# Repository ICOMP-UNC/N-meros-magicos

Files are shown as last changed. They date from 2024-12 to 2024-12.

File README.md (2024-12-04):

# N-meros-magicos
## Control automático de compuerta y monitoreo del entorno

Este proyecto consiste en el control automático de una compuerta a través de un sensor de temperature, configurable mediante comunicación UART.

El control de la compuerta se realiza por medio de un motor paso a paso a lazo abierto.
El monitoreo del entorno se realiza por medio de un sensor de temperatura
La comunicación por UART permite el control de la compuerta, la configuración del funcionamiento del automatismo y la lectura del historial de temperaturas registradas por el sensor.

El proyecto fue diseñado originalmente para un microcontrolador LPC1769, aunque debió ser migrado durante el desarrollo a STM32F103CB, debido a la falta de disponibilidad del primer micro.

### Escenario
En un depósito de sustancias peligrosas se busca tener el control de una compuerta que permita mantenerla cerrada si la temperatura dentro del depósito es muy alta. En este caso, el automatismo debe accionar los mecanismos para enfriar el ambiente, siendo solo posible abrir la compuerta mediante un comando especial.

En cambio, si la temperatura está dentro del rango normal, la compuerta puede ser operada por medio de un switch local o desde una consola a distancia.

En cualquier caso la consola a distancia puede solicitar el estado de la compuerta y del sensor de temperatura

### Requerimientos

- Al iniciar el automatismo, debe verificar que la compuerta no presente obstáculos y tenga libre movimiento.
- Si la temperatura se encuentra dentro de un rango predefinido, la compuerta puede abrir o cerrarse con un mismo pulsador
- Si la temperatura supera el nivel de alerta, debe encenderse un enfriador,
- Si la temperatura supera el nivel máximo, debe encenderse la alarma sonora
- Si la temperatura supera el nivel crítico, debe cerrarse y bloquear la puerta, impidiendo que pueda abrirse local o remotamente
- Por seguridad, una vez bloqueada la puerta, solo puede volver a abrirse a través de una switch especial.
- Una consola externa debe poder monitorear permanentemente el estado del automatismo y operar la compuerta, excepto cuando la temperatura supere el nivel crítico.

### Diagrama de flujo del automatismo en general

```mermaid

flowchart
    A[Inicio] -->B[Inicializar motor]
    B --> C{Inicializacion ok?}
    C -->|No| E[Encender Alarma sonora y Luz de motor parpadenante]
    E --> I[Bucle infinito]
    I --> I
    C -->|Si| D[Abrir compuerta]
    D -->G[Habilitar sensor]
```

### Diagrama de flujo del sensor de temperatura

```mermaid
flowchart
    Sample[Tomar muestra] -->temp_ok{Temperatura mayor a TEMP_ALERTA?}
    temp_ok -->|No| enable_manual_mode[Habilitar operacion manual]
    temp_ok -->|Si| cooler_on[Encender enfriador]

    cooler_on -->is_temp_high{Temperatura mayor a TEMP_MAX?}
    is_temp_high-->|Si|alarm_on[Encender alarma sonora]
    alarm_on-->open_door[Abrir puerta]
    open_door-->notify[Notificar a consola]
    notify -->is_temp_critical{Temperatura mayor a TEMP_CRITICAL?}
    is_temp_critical-->|Si|lock[Cerrar y bloquear puerta]
```

### Diagrama de flujo de la rutina de inicio del motor

```mermaid
flowchart
    start[Rutina de inicio] -->move_left[Mover a izquierda]
    move_left-->sw_left{Sw izquierdo encontrado?}
    sw_left-->|si| move_right[Mover a derecha]
    sw_left-->|no| error[Fallo de inicio]
    move_right-->sw_right{Sw derecho encontrado?}
    sw_right-->|si| open_door[Abrir puerta]
    open_door-->Fin[Fin de rutina OK]
    sw_right-->|no| error[Fallo de inicio]

```

### Hardware necsario para la implementación

- Placa de desarrollo STM32F103CB
- Motor paso a paso 28BYJ-48 5v
- Driver para motor paso a paso ULN2003
- Sensor de temperatura LM35 (o potenciometro)
- Buzzer pasivo
- 2 Switches para fin de carrera
- 1 Switch para accionamiento manual
- 2 diodos LED
- 2 resistencias 220 ohms
- Módulo conversor serie TTL a USB
- PC con comunicación serie (se provee script menu.py)

### Diagrama de conexionado

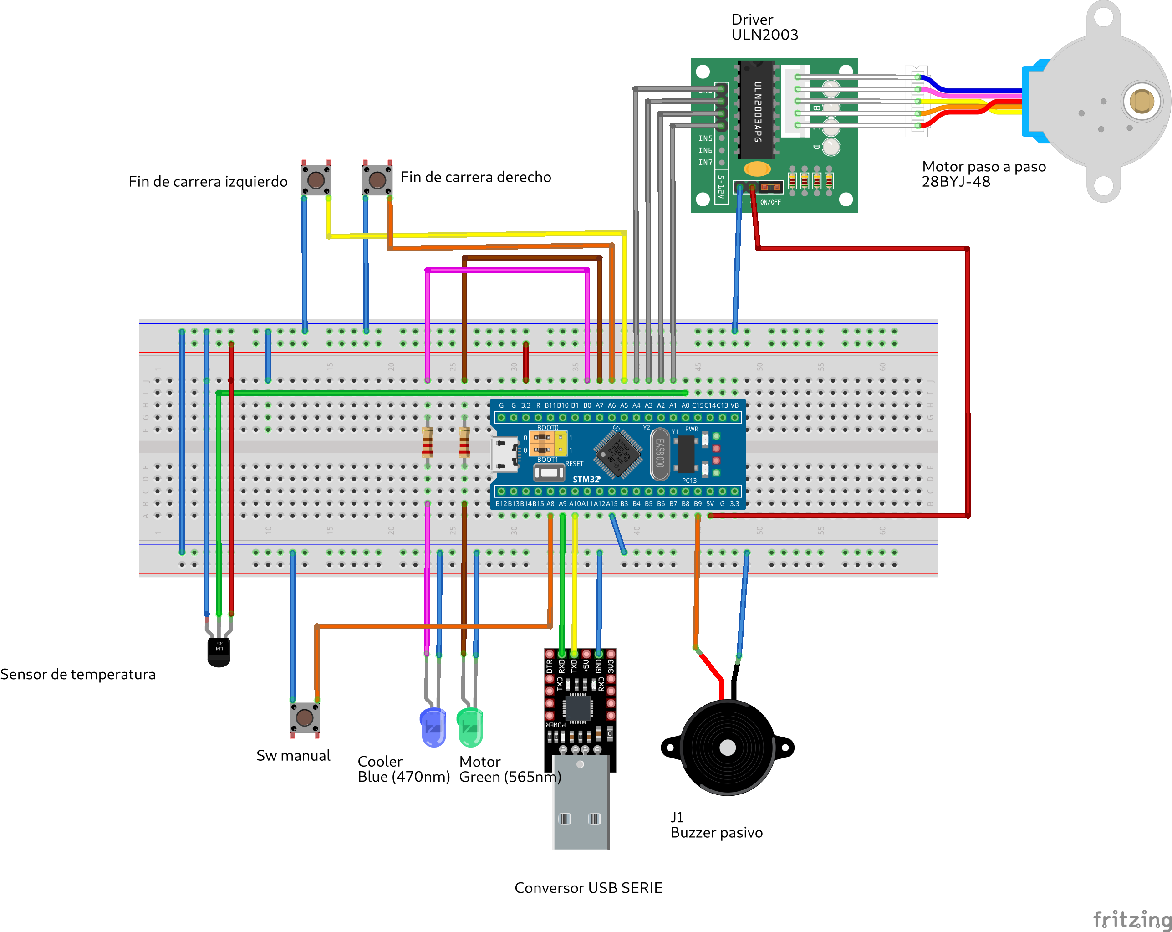
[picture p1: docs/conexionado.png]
alt text for screen readers Conexionado


### Presentación
[Enlace con la presentación del proyecto](https://www.youtube.com/watch?v=D4o0tx2uYDA)

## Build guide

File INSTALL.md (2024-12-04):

### Instalación
## Control automático de compuerta y monitoreo del entorno
### Pre requisitos
Deben estar instalados:

- VSCode
- Platformio
- ST-Link debugger
- Placa de desarrollo STM32F103CB

### Descargar repositorio

`git clone https://github.com/ICOMP-UNC/N-meros-magicos.git`

Abrir proyecto en VSCode-platformio. El archivo de configuración de proyecto se encuentra en `N-meros-magicos/platformio.ini`.

Para compilar el proyecto desde platformIO Core CLI:
`pio run`

Para subir el firmware a la placa desde platformIO Core CLI:
`pio run -t upload`

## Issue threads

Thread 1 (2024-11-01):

Final Project Task - Embedded System Development

GabrielEValenzuela, 2024-11-01:
This project will involve designing and implementing an embedded system in a collaborative GitHub environment. Each team of 4 students will follow a structured approach to plan, design, document, and implement the project. Below are the steps and expectations for each part of the project.

### Task Breakdown

#### 1. **Project Plan and Milestones**

   - **Objective**: Develop a comprehensive project plan outlining all key stages, goals, and milestones.
   - **Deliverables**:
     - A high-level project description (one paragraph).
     - Define the main objectives and success criteria for the project.
     - Create a timeline and assign tasks to each team member.
     - Include a checklist or Kanban-style board in GitHub Projects to track task progress. (Optional)

#### 2. **System Design Documentation**

   - **Objective**: Outline the design of the embedded system to ensure that all team members understand the structure and functionality.
   - **Deliverables**:
     - Block diagrams or flowcharts representing the system architecture.
     - State diagrams or flow diagrams for critical functions or states.
     - Define the main modules, their purpose, and how they interact.
     - Describe the communication between different components, especially if peripherals like ADC, DAC, GPIO, or other sensors are used.

#### 3. **Implement Continuous Integration and Continuous Deployment (CI/CD)** _(if applicable)_

   - **Objective**: Set up a CI/CD pipeline to automate the build and test process.
   - **Deliverables**:
     - Configure GitHub Actions to automatically build the code upon each pull request.
     - Integrate code quality checks using `clang-format` to enforce consistent coding style.
     - Configure unit tests and static analysis tools to catch potential issues early.  (Optional)

#### 4. **Code Implementation and Style Guidelines**

   - **Objective**: Implement the code with a consistent and professional style, documented thoroughly.
   - **Deliverables**:
     - Write clean, modular code that adheres to best practices and utilizes meaningful variable and function names.
     - Run `clang-format` on all code to ensure consistent styling across the project.
     - Make use of comments for code clarity and readability.

#### 5. **Comprehensive Documentation with Doxygen**

   - **Objective**: Ensure the code is thoroughly documented for ease of understanding and maintainability.
   - **Deliverables**:
     - Document all functions, modules, and key variables using Doxygen-style comments.
     - Provide a README.md that explains the overall functionality of the code, lists team members, and includes any general notes about the codebase.
     - Use Doxygen to generate HTML documentation and commit it to a `docs/` directory for easy access.

#### 6. **INSTALL.md - Installation and Setup Guide**

   - **Objective**: Provide a clear and detailed guide for building, flashing, and running the firmware on the target hardware.
   - **Deliverables**:
     - Instructions on how to compile the code, including any specific tools or dependencies required.
     - Detailed steps for flashing the firmware onto the target hardware (e.g., using OpenOCD, ST-Link, or other tools).
     - Information about supported platforms, such as operating systems and specific microcontroller details.

#### 7. **Hardware Specifications and Schematics**

   - **Objective**: Provide all relevant details about the hardware configuration and connections.
   - **Deliverables**:
     - A brief overview of the hardware used (microcontroller type, sensors, actuators, etc.).
     - Circuit schematics in image or SVG format that detail the connections of all components.
     - A hardware setup guide describing how components should be physically connected.

#### 8. **Additional Suggestions**

   - Use Git internal branches for each feature or module, and merge them only when reviewed and approved by at least two team member and team leader.
   - Create a branch `1.0.0` considered the release branch, and merge **only when reviewed and approved by professor.**
   - **DO NOT MERGE TO MASTER OR MAKE COMMIT DIRECTLY**
   - Apply good practices of software engineering.
   - Consider creating an Issue Tracker for each task and keep the conversation within the comments to log progress.
   - Make use of GitHub's Wiki or Project Board features to organize and visualize the workflow.

### Final Deliverable

The project should be fully implemented, tested, and documented. Each team will create a GitHub repository with all code, diagrams, and documentation completed and structured as per the requirements above. Ensure that the `README.md` provides a quick overview and instructions to navigate the repository effectively.

Good luck, and remember that collaboration and clear communication are key to a successful project! 🍀

---

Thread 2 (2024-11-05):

Estructura inicial

horacioruedaunc, 2024-11-05:
En la rama `develop` se encuentra la estructura inicial del proyecto, a partir de la cual se deberán crear las ramas necesarias para cada feature. Ya cuenta con la librería CMSIS y drivers. Cuando una feature esté finalizada mergeamos a `develop`

Dentro del archivo `app.c` se definen dos funciones:

`APP_init`: donde se inicializarán los módulos
`APP_loop`: donde se llamarán las funciones dentro del bucle principal

Closed 2024-11-12.

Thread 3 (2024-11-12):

Migración a stm32

horacioruedaunc, 2024-11-12:
Debido a la falta de disponibilidad de la placa lpc1769, se portará el proyecto a stm32

horacioruedaunc, 2024-11-14:
Finalizado el port del estado actual del proyeco a stm32. Se continua con el desarrollo de features desde este punto

Closed 2024-11-14.

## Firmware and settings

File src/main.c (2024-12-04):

/*
===============================================================================
 Name        : ed3_integrador.c
 Author      : Horacio Rueda
 Version     :
 Copyright   : $(copyright)
 Description : Aplicación que controla un motor paso a paso por medio de
               Interfaz UART con monitoreo de sensor de temperatura
===============================================================================
*/

#include "app.h"

int main(void)
{
    APP_init();

    while (1)
    {
        APP_loop();
    }
    return 0;
}

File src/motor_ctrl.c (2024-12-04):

/*
 * motor_ctrl.c
 *
 *  Created on: Jun 14, 2024
 *      Author: Horacio
 */

/********************************************************************
 *                      INCLUSIONES
 ********************************************************************/

#include "motor_ctrl.h"
#include "comm_uart.h"
#include "output.h"
#include "port.h"
#include "stdio.h"

/********************************************************************
 *                      DEFINICIONES
 ********************************************************************/

#define MOTOR_STATUS_LIMIT_1 0x0001
#define MOTOR_STATUS_LIMIT_2 0x0002

#define STEP_TIMEOUT_HIGH     2
#define STEP_TIMEOUT_MED      4
#define STEP_TIMEOUT_LOW      8
#define START_ROUTINE_TIMEOUT 30000
#define LED_TIMEOUT           200

/********************************************************************
 *                      ENUMERADOS
 ********************************************************************/

typedef enum
{
    EV_START_ROUTINE,
    EV_OPEN,
    EV_CLOSE,
    EV_STOP,
    EV_FINISH_MOVE,
    EV_TIMEOUT,
    EV_NONE,
} MOTOR_events_t;

typedef enum
{
    DIR_LEFT,
    DIR_RIGHT,
} MOTOR_dir_t;

enum
{
    SIGNAL_1,
    SIGNAL_2,
    SIGNAL_3,
    SIGNAL_4,
};
/********************************************************************
 *                      STRUCTS
 ********************************************************************/

/********************************************************************
 *                      VARIABLES LOCALES
 ********************************************************************/

static MOTOR_states_t current_state;
static MOTOR_events_t evt;
static uint16_t status;
static int32_t initial_pos;
static int32_t target_pos;
static int32_t offset_pos;
static int32_t final_pos;
static int32_t current_absoulute_pos;
static int32_t limit_1_pos;
static int32_t limit_2_pos;
static uint8_t step;
static uint32_t step_timer;
static uint32_t step_timeout;
static uint32_t start_routine_timer;
static uint32_t led_timer;
/********************************************************************
 *                      PROTOTIPO FUNCIONES LOCALES
 ********************************************************************/

/********************************************************************
 *                      FUNCIONES LOCALES
 ********************************************************************/

static void motor_on(void)
{
    int steps_matrix[4][4] =
        //  T1, T2, T3, T4
        {{1, 0, 0, 0},  // SIGNAL_1
         {0, 1, 0, 0},  // SIGNAL_2
         {0, 0, 1, 0},  // SIGNAL_3
         {0, 0, 0, 1}}; // SIGNAL_4

    if (steps_matrix[SIGNAL_1][step])
        PORT_motor_signal_1_on();
    else
        PORT_motor_signal_1_off();

    if (steps_matrix[SIGNAL_2][step])
        PORT_motor_signal_2_on();
    else
        PORT_motor_signal_2_off();

    if (steps_matrix[SIGNAL_3][step])
        PORT_motor_signal_3_on();
    else
        PORT_motor_signal_3_off();

    if (steps_matrix[SIGNAL_4][step])
        PORT_motor_signal_4_on();
    else
        PORT_motor_signal_4_off();

    PORT_led_on();
}

static void motor_off(void)
{
    PORT_motor_signal_1_off();
    PORT_motor_signal_2_off();
    PORT_motor_signal_3_off();
    PORT_motor_signal_4_off();
    evt = EV_FINISH_MOVE;
}

static void motor_move(MOTOR_dir_t dir)
{
    motor_on();
    if (dir == DIR_LEFT)
    {
        if (step_timer == 0)
        {
            step_timer = step_timeout;
            step--;
            current_absoulute_pos--;
            if (step == 0xFF)
                step = 3;
        }
    }
    else if (dir == DIR_RIGHT)
    {
        if (step_timer == 0)
        {
            step_timer = step_timeout;
            step++;
            current_absoulute_pos++;
            if (step == 4)
                step = 0;
        }
    }
}

void motor_move_to_pos(int32_t relative_pos)
{
    int32_t error, pos;
    pos = relative_pos + offset_pos;

    error = pos - current_absoulute_pos;
    if ((error > 0 && error < POS_ERROR) || (error < 0 && (-error) < POS_ERROR))
    {
        evt = EV_FINISH_MOVE;
        return;
    }

    if (pos > current_absoulute_pos)
    {
        evt = EV_NONE;
        motor_move(DIR_RIGHT);
    }

    if (pos < current_absoulute_pos)
    {
        evt = EV_NONE;
        motor_move(DIR_LEFT);
    }
}

static void move_fsm(void)
{
    MOTOR_states_t next_state;
    next_state = current_state;

    switch (current_state)
    {
        case MOTOR_IDLE:
            switch (evt)
            {
                case EV_START_ROUTINE:
                    step_timer = step_timeout;
                    status = 0;
                    current_absoulute_pos = 0;
                    start_routine_timer = START_ROUTINE_TIMEOUT;
                    next_state = MOTOR_START_ROUTINE;
                    break;
                case EV_OPEN:
                    target_pos = initial_pos;
                    next_state = MOTOR_MOVING;
                    break;
                case EV_CLOSE:
                    target_pos = final_pos;
                    next_state = MOTOR_MOVING;
                    break;
                case EV_STOP: next_state = MOTOR_STOPPING; break;
                case EV_NONE:
                case EV_FINISH_MOVE: break;

                default: break;
            }
            break;
        case MOTOR_START_ROUTINE:
            switch (evt)
            {
                case EV_FINISH_MOVE: next_state = MOTOR_IDLE;
                case EV_STOP: next_state = MOTOR_STOPPING; break;
                case EV_TIMEOUT:
                    next_state = MOTOR_ERROR;
                    COMM_UART_motor_error();
                    motor_off();
                    OUTPUT_set_buzzer_level(2);
                    OUTPUT_buzzer_on();
                    break;
                default: break;
            }
            break;
        case MOTOR_MOVING:
            switch (evt)
            {
                case EV_FINISH_MOVE: next_state = MOTOR_IDLE;
                case EV_STOP: next_state = MOTOR_STOPPING; break;
                default: break;
            }
            break;
        case MOTOR_STOPPING:
            switch (evt)
            {
                case EV_FINISH_MOVE: next_state = MOTOR_IDLE; break;
                default: break;
            }
            break;

        default: break;
    }
    current_state = next_state;
    evt = EV_NONE;
}
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

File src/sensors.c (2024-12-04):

/*
 * sensors.c
 *
 *  Created on: Jun 14, 2024
 *      Author: Horacio
 */

/********************************************************************
 *                      INCLUSIONES
 ********************************************************************/
#include "sensors.h"
#include "comm_uart.h"
#include "motor_ctrl.h"
#include "output.h"
#include "port.h"
#include "stdio.h"
#include <libopencm3/cm3/nvic.h>
#include <libopencm3/stm32/adc.h>
#include <libopencm3/stm32/dma.h>
#include <libopencm3/stm32/gpio.h>
#include <libopencm3/stm32/rcc.h>
#include <libopencm3/stm32/timer.h>

/********************************************************************
 *                      DEFINICIONES
 ********************************************************************/
#define ADC_CHANNEL_TEMP_SENSOR ADC_CHANNEL0

#define WARNING_TEMP  15
#define MAX_TEMP      50
#define CRITICAL_TEMP 80

#define HISTORY_SIZE 30
#define TRUE         1

/********************************************************************
 *                      ENUMERADOS
 ********************************************************************/
enum
{
    TEMP_LOW,
    TEMP_HIGH,
};

/********************************************************************
 *                      STRUCTS
 ********************************************************************/

/********************************************************************
 *                      VARIABLES LOCALES
 ********************************************************************/

static uint8_t head;
static uint8_t tail;
static uint8_t size;

float temp_history[HISTORY_SIZE];
static uint8_t status;

/********************************************************************
 *                      PROTOTIPO FUNCIONES LOCALES
 ********************************************************************/
void adc_init(void);
void timer2_init(void);
void dma_init(void);

/********************************************************************
 *                      FUNCIONES LOCALES
 ********************************************************************/

void adc_init(void)
{
    /* Enable ADC1 clock */
    rcc_periph_clock_enable(RCC_ADC1);
    rcc_periph_clock_enable(RCC_GPIOA);

    /* Configure ADC1 */
    adc_power_off(ADC1);
    adc_disable_scan_mode(ADC1);
    adc_set_continuous_conversion_mode(ADC1);
    adc_disable_external_trigger_regular(ADC1);
    adc_set_right_aligned(ADC1);
    adc_set_sample_time(ADC1, ADC_CHANNEL_TEMP_SENSOR, ADC_SMPR_SMP_55DOT5CYC); /* Set sample time */

    /* Calibrate ADC1 */
    adc_power_on(ADC1);
    adc_reset_calibration(ADC1);
    adc_calibrate(ADC1);
}

void timer2_init(void)
{
    /* Enable Timer 2 clock */
    rcc_periph_clock_enable(RCC_TIM2);

    /* Enable TIM2 interrupt. */
    nvic_enable_irq(NVIC_TIM2_IRQ);

    /* Reset TIM2 peripheral to defaults. */
    rcc_periph_reset_pulse(RST_TIM2);

    /* Set timer prescaler for 1Hz (1 tick per second) */
    timer_set_prescaler(TIM2, 7200 - 1);
    timer_set_period(TIM2, 10000 - 1);

    /* Enable Timer 2 interrupt for periodic triggering */
    timer_enable_irq(TIM2, TIM_DIER_UIE);

    /* Start the timer */
    timer_enable_counter(TIM2);
}

void dma_init(void)
{
    /* Enable DMA1 clock */
    rcc_periph_clock_enable(RCC_DMA1);

    /* Reset DMA1 stream */
    dma_channel_reset(DMA1, DMA_CHANNEL1);

    /* Set DMA configuration */
    dma_set_peripheral_address(DMA1, DMA_CHANNEL1, (uint32_t)&ADC_DR(ADC1)); /* ADC data register */
    dma_set_memory_address(DMA1, DMA_CHANNEL1, (uint32_t)&TIM_CCR4(TIM3));   /* Memory buffer */
    dma_set_number_of_data(DMA1, DMA_CHANNEL1, 1);                           /* Number of data items */
    dma_set_priority(DMA1, DMA_CHANNEL1, DMA_CCR_PL_LOW);
    dma_set_memory_size(DMA1, DMA_CHANNEL1, DMA_CCR_MSIZE_16BIT);     /* Memory size: 16 bits */
    dma_set_peripheral_size(DMA1, DMA_CHANNEL1, DMA_CCR_PSIZE_16BIT); /* Peripheral size: 16 bits */
    dma_enable_memory_increment_mode(DMA1, DMA_CHANNEL1);
    dma_enable_circular_mode(DMA1, DMA_CHANNEL1); /* Enable circular mode */

    /* Start DMA transfer */
    dma_enable_channel(DMA1, DMA_CHANNEL1);

    /* Enable ADC DMA mode */
    adc_enable_dma(ADC1);

    adc_start_conversion_direct(ADC1);
}

float get_temperature(uint16_t adc_read)
{
    float ret = ((float)adc_read * 330.0 / 3 / 4096.0);
    return ret;
}

void tim2_isr(void)
{
    if (timer_get_flag(TIM2, TIM_SR_UIF))
    {
        timer_clear_flag(TIM2, TIM_SR_UIF); // Clear update interrupt flag

        float temp = get_temperature(adc_read_regular(ADC1));
        if (temp > CRITICAL_TEMP)
        {
            if (status == TEMP_LOW)
            {
                COMM_UART_temp_alarm();
                status = TEMP_HIGH;
            }
            OUTPUT_set_buzzer_level(100);
            OUTPUT_buzzer_on();
            OUTPUT_cooler_on();
            MOTOR_CTRL_close();
        }
        else if (temp > MAX_TEMP)
        {
            if (status == TEMP_LOW)
            {
                COMM_UART_temp_alarm();
                status = TEMP_HIGH;
            }
            OUTPUT_cooler_on();
            OUTPUT_buzzer_on();
            MOTOR_CTRL_open();
        }
        else if (temp > WARNING_TEMP)
        {
            OUTPUT_cooler_on();
            OUTPUT_buzzer_off();
        }

        else
        {
            if (status == TEMP_HIGH)
            {
                COMM_UART_temp_ok();
                status = TEMP_LOW;
            }
            OUTPUT_buzzer_off();
            OUTPUT_cooler_off();
        }

        temp_history[head] = temp;

        if (size < HISTORY_SIZE)
            size++;
        else
            tail++;

        head++;
        head = head % HISTORY_SIZE;
        tail = tail % HISTORY_SIZE;
    }
}

/********************************************************************
 *                      FUNCIONES GLOBALES
 ********************************************************************/

void SENSORS_init(void)
{
    adc_init();
    dma_init();
    timer2_init();
}

uint16_t SENSORS_read_temp_history(char* buffer)
{
    uint8_t size_aux = size;
    uint8_t tail_aux = tail;
    size_t len = 0;
    int8_t pos;
    float temp;
    for (uint8_t i = 0; i < size_aux; i++)
    {
        pos = tail_aux + i;
        pos = pos % HISTORY_SIZE;

        temp = temp_history[pos];
        len += sprintf(buffer + len, "%d.%d°, ", (int32_t)temp, (int32_t)(temp * 10) % 10) - 1;
    }
    buffer[len] = '\n';
    len++;
    buffer[len] = 0;
    return len;
}

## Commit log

2024-11-07 add, menu de configuracion
2024-11-08 add manejo de entrada y salida
2024-11-08 add señales y switches
2024-11-08 llamadas en la app principal
2024-11-12 port a stm32
2024-11-13 fix uart functions
2024-11-13 add systick timer
2024-11-14 fix led gpio number
    [port.h]
2024-11-15 add sensor analogico
2024-11-15 update menu para obtener lecturas de sensor
2024-11-15 update matriz y se enciende led indicador de movimiento
2024-11-15 add mensaje de alerta por temperatura
2024-11-15 add señal para activar el cooler
2024-11-16 add error en motor inicializacion
    [comm_uart.c, motor_ctrl.c]
2024-11-16 add switch de modo manual
2024-11-16 nivel de sonido en alarma
2024-11-16 cooler tiene intensidad variable en funcion de temperatura
2024-11-16 fix tamaño de array y retardos
    [isr.c, sensors.c]
2024-11-16 script de consola
2024-11-16 add diagrama de conexionado
    [conexionado.fzz]
2024-11-16 add comando para conocer estado de compuerta
